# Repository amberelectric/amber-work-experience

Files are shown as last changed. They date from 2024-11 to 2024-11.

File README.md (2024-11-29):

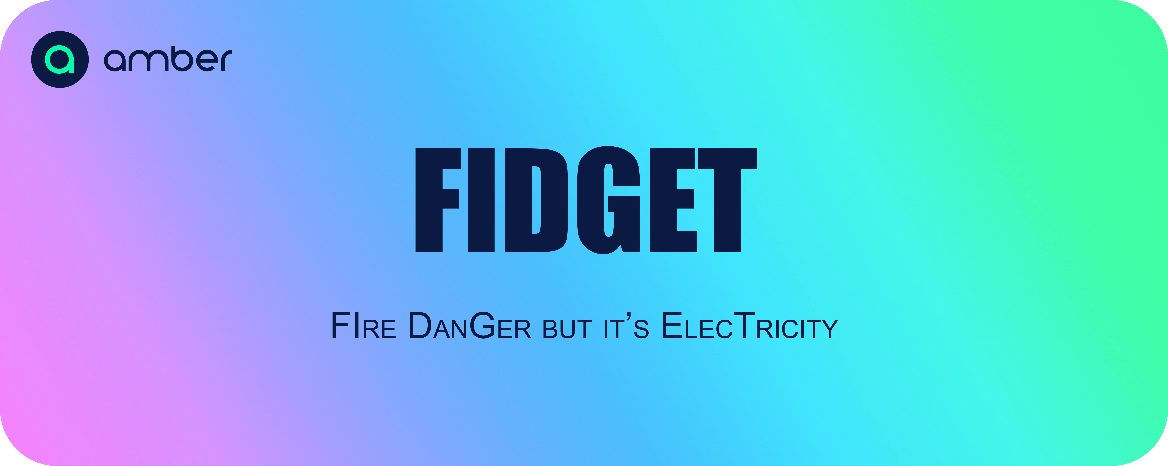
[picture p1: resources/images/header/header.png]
Amber FIDGET - Fire Danger but it's Electricity


# Intro / Say What Now?!

### What is it an what does it do?
The Amber FIDGET is a miniature Fire Danger Rating sign that displays the current power price descriptor for your house.

### How does it do it?
The FIDGET connects to your Wi-Fi network
and uses the [Amber API](https://app.amber.com.au/developers/documentation/)
to fetch the current price descriptor for your property.
It then translates this into a fire danger rating, and tells a servo motor to point at that rating, with 'tweening'.

# Build Guide

## Parts

### Owned
These parts are only needed to **make** the FIDGET. They are not required once it's running
- Computer (preferably should turn on)
- Hot Glue Gun
- 2D Printer
- 3D Printer (Not necessary. You can just tape or hot glue the components together.)
- Box Cutter
- Hair Dryer (I'll explain I promise)

### Purchased
Links are provided for Core Electronics, a Newcastle-based electronics provider with generally pretty good prices.
- [ESP32-C3 WROOM Dev Board](https://core-electronics.com.au/esp32-c3-wroom-development-board.html) (Or any other ESP32 board)
- [9g Micro Servo](https://core-electronics.com.au/feetech-fs90-1-5kgcm-micro-servo-9g.html) (Or any 9g servo with half-decent torque)
- [Male to Female Jumper Wires](https://core-electronics.com.au/jumper-wires-premium-12-m-f-pack-of-10.html) (Any wire will work but jumpers are nicer)
- [USB Micro-B Cable](https://core-electronics.com.au/usb-cable-type-a-to-micro-b-1m.html) (Once the FIDGET is running, it's possible to power it off a battery pack)

### Printed In Two Dimensions
The front of the sign has to be printed (or you can draw it, I guess).
If you have a colour printer, use `resources/images/sign/sign colour.png`.
Otherwise, use `resources/images/sign/sign bw.png` and colour in the sections with a pen or highlighter.

### Printed In Three Dimensions
Note: These parts are not strictly necessary, but they make putting together and pulling apart the FIDGET much easier.

The files you need to print are in the `resources/objects` folder.
`fire danger sign.f3d` is the Fusion 360 model for the entire FIDGET, and `fire danger sign.stl` is the whole model.
You only need to print `arrow.stl`, `servo bottom.stl`, `servo top.stl` and `esp32.stl`.

When printing, bigger layer heights are recommended to increase strength.

### Materials
- Cardboard box of regular thickness
- Hot glue
- Regular glue (tape will work too)
- Rubber band (a cable tie will work too)

## Make

### 1. Cut the Sign Cardboard
Use the box cutter to cut a piece of blank cardboard about half a centimeter bigger than the sign on all sides,
as shown in the picture below:

Cardboard cut about half a centimeter bigger than the sign on all sides

Then, align the sign in the center of the cardboard and glue it on.
Regular (non-hot) glue is preferable as it allows the paper to lie flush on the cardboard.

### 2. Wiring
The servo motor has to be connected to the ESP32 as follows:

| ESP32 Pin | Servo Pin |
|---|---|
| GND | - (Brown wire) |
| 5V | + (Red wire) |
| 0 | Signal (Orange wire) |

Note that you can use any of the GND or 5V pins on the ESP32.

### 3. Mount the Servo
To mount the servo on the sign you need to do a few things:
1. Use something sharp and pointy (pen, box cutter, scissors, drill, hole punch, etc) to punch a hole in the front of the sign where the servo will stick out.
2. If you 3D printed `servo top.stl` and `servo bottom.stl`:
   1. Place the servo inside `servo bottom`.
   2. Place `servo top` on top.
   3. Make sure the servo wire is out the side of the case, and the front of the servo protrudes from the front of the case.
   4. Carefully hot glue or melt the two halves of the servo case together, making sure not to get glue on the servo within.
3. Glue the servo case on to the back of the sign, so that the wires point to the left and the front of the servo goes through the hole in the sign.

The attached servo should look like the below image:

Mounted servo motor

### 4. Attach the Arrow
Turning around to the front of the sign, you can now attach the arrow to the servo motor.
In the bag of hardware that comes with the servo motor, there are five "horns" (pieces of plastic that attach to the gear on the front of the servo), one small screw and two large screws.

1. Make sure the servo is at 0˚. (Use the code at the end of this step)
2. Attach the **shortest** servo horn to the servo gear, pointing directly to the right. Note that it doesn't have to be pointing exactly right. You can adjust the angles it points to easily at the top of `main.cpp`.  
3. Screw the horn in place with the small screw.
4. Hot glue the arrow onto the horn.

To set the servo to 0˚, use the following code:
```c++
#include <ESP32_New_ISR_Servo.h>

void setup() {
  ESP32_ISR_Servos.useTimer(0);  // Use timer 0
  int servoIndex = ESP32_ISR_Servos.setupServo(0, 500, 2500);  // Start the servo on pin 0
  ESP32_ISR_Servos.setPosition(servoIndex, 0);  // Set the servo to 0˚
}

void loop() {}
```

The attached arrow should look like the below images:

Attached arrow
Attached arrow

### 5. Attach the ESP23
Attaching the ESP32 is fairly simple.
If you printed the ESP32 mount, hot glue it on the back of the FIDGET to the left, and clip in the ESP32.
If you didn't simply glue or tape the ESP32 in place.

Note:
The 3D printed mount may not fit perfectly.
Test it before you hot glue it in place and then bend the arms while they're hot from the glue.

The attached ESP32 should look like the below image:

Mounted ESP32

### 6. Finishing touches
Use a rubber band to hold the wires together neatly.
I feel like you shouldn't need an image for this one...

Then, cut out some more cardboard and hot glue it into a stand shape, like this:

FIDGET Stand

The design is primarily up to your imagination/engineering, but you should add a cross-beam to stop the cardboard from bending.

### 7. You did it!!
Congratulations!
You built the Amber FIDGET without blowing anything up!
Behold, the final product.
(The paperclip is because I had glue issues.)

Finished FIDGET
Finished FIDGET

# (Quick) Start

### Prerequisites
The only prerequisite for FIDGET is [PlatformIO Core](https://docs.platformio.org/en/latest/core/installation/index.html), a CLI for interfacing with the ESP32.

### Secrets file
FIDGET uses the Amber API to fetch the current price descriptor.
In order to accomplish this, you must have your WiFi and API credentials stored in `src/secrets.h`.
An example is provided below.

```c++
#define WIFI_SSID "[YOUR SSID]"
#define WIFI_PASSKEY "[YOUR PASSWORD]"
#define API_KEY "[YOUR API KEY]"
#define SITE_ID "[YOUR SITE ID]"
```

To find your Site ID, run the following command and look for the `id` key.

```sh
curl -H "Authorization: Bearer [YOUR API KEY]" https://api.amber.com.au/v1/sites
```

Note: If you are using the debug server, you must add the following line to `secrets.h` as well.

```c++
#define DEBUG_HOST "[YOUR IP ADDRESS OR HOSTNAME]"
```

### Quick Run
To quickly upload the code to the FIDGET, connect the ESP32 to your computer, then run `resources/scripts/upload.sh`.

# Usage

## Running the Code
Multiple scripts are provided in `resources/scripts`.
Each one serves a specific purpose:
- `compile.sh` checks that your code can be compiled for the ESP32 but does not upload the code.
- `upload.sh` compiles and uploads your code to the ESP32, then opens a serial monitor in your terminal.
- `debug.sh` starts the debugging server on your device.

Note:
Both `compile.sh` and `upload.sh` automatically install all required libraries via [the PlatformIO registry](https://registry.platformio.org).

## Troubleshooting

### Debug Server
To use the debug server, run `resources/debugServer.sh`, then enter your credentials when prompted.
This script will copy real-time data from the Amber API into `resources/v1/sites/[YOUR SITE ID]/prices/current`,
then start a local web server on port 8000 with Python's `http.server`.

On the ESP32 side,
all you need to do is define `DEBUG_HOST` in `secrets.h` (see "Secrets File")
and uncomment this line near the start of `main.cpp`:
```c++
#define USE_DEBUG_SERVER
```

## Logging
The following table shows the status messages displayed on the ESP32 LED and in the Serial Monitor.
A description of the state is in the `Status` column,
the LED colour and Serial output are shown in the next two columns,
and the final column shows the minimum required log level to show the state.

| Status | LED Colour | Print Statement | Level |
|---|---|---|---|
| Connecting to Wi-Fi | Yellow | Connecting to Wi-Fi... | Info |
| Setting Clock | Green | Setting time... | Info |
| Fetching Descriptor | Cyan | Fetching descriptor... | Info |
| Fetching Debug Descriptor | Blue | Fetching descriptor from debug server... | Info |
| Moving Servo | Purple | Updating servo... | Debug |
| Idle | White | Done! | Info |
| **Errors** | **Red-...** | | |
| Could not connect to Wi-Fi | Red-Red | Could not connect to Wi-Fi | Warning |
| Could not connect to the API | Red-Yellow-Red | Could not connect to API | Error |
| Could not configure API | Red-Yellow-Yellow | Could not configure API | Error |
| API timed out | Red-Yellow-Green  | API connection timed out | Error |
| API gave invalid response | Red-Yellow-Cyan | API returned invalid response | Error |
| HTTP status code error | Red-Green-Red | API returned error code: [CODE] | Error |
| HTTP could not skip headers | Red-Green-Yellow  | Could not skip HTTP headers: [CODE] | Error |
| Could not parse JSON | Red-Cyan-Red | Could not parse returned JSON | Error |
| Could not find general channel | Red-Cyan-Yellow | Could not find general channel in JSON | Error |
| Servo could not start | Red-Blue | Could not start servo | Fatal |
| Debug API not provided | Red-Purple | Debug API URL not provided. Using Amber API. | Warning |

Notes
1. Where more than one colour is listed in the `LED Colour` column,
   the LED will flash the colours in sequence with a 300ms delay.
2. The LED will show the appropriate colour no matter what the log level is set to.
3. If the `Level` is `Fatal`, the program will stop and the LED will flash the pattern repeatedly with a one second break.

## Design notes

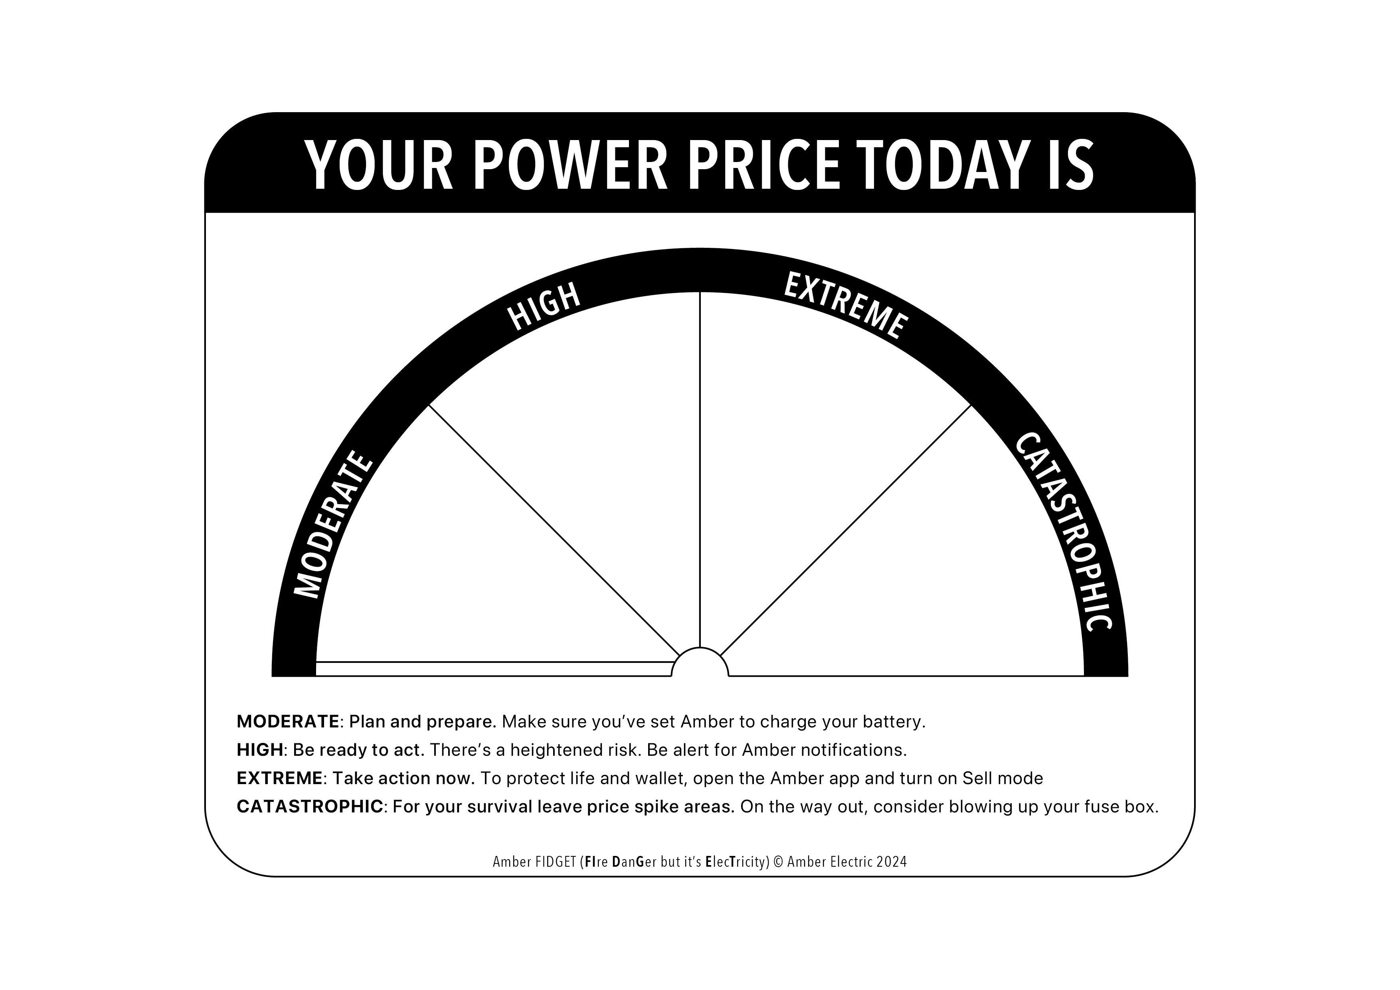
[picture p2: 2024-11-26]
resources/images/sign/sign bw.png

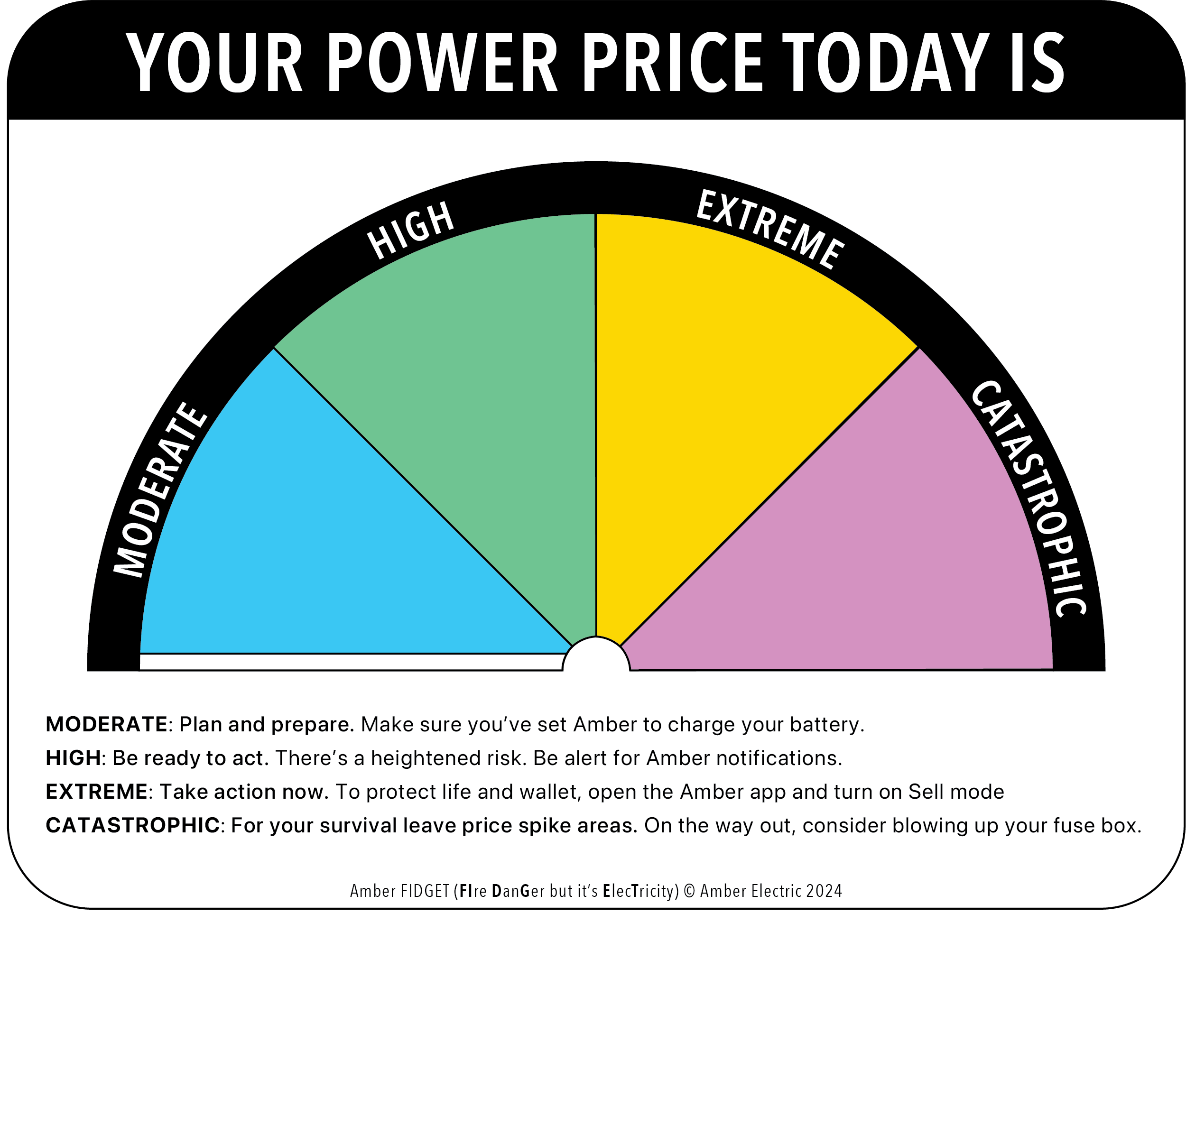
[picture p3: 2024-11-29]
resources/images/sign/sign colour.png

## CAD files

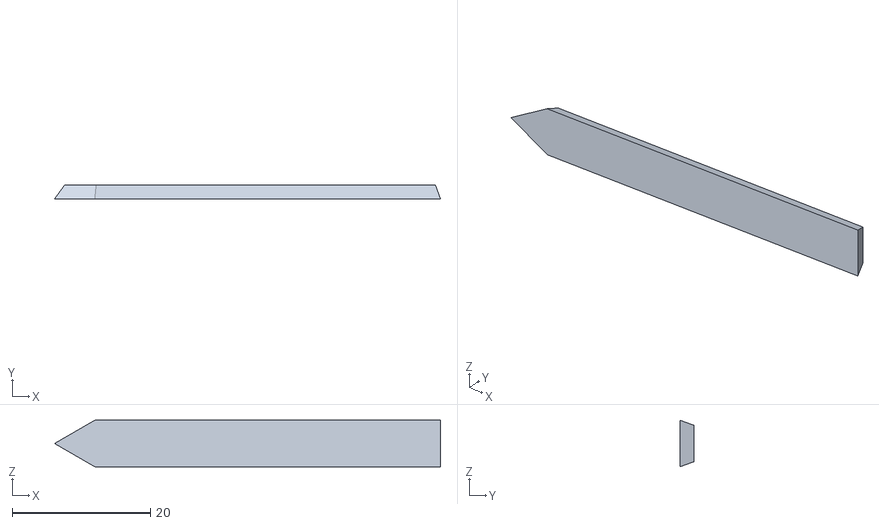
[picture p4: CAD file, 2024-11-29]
resources/objects/arrow.stl
55.8 x 2.00 x 6.73

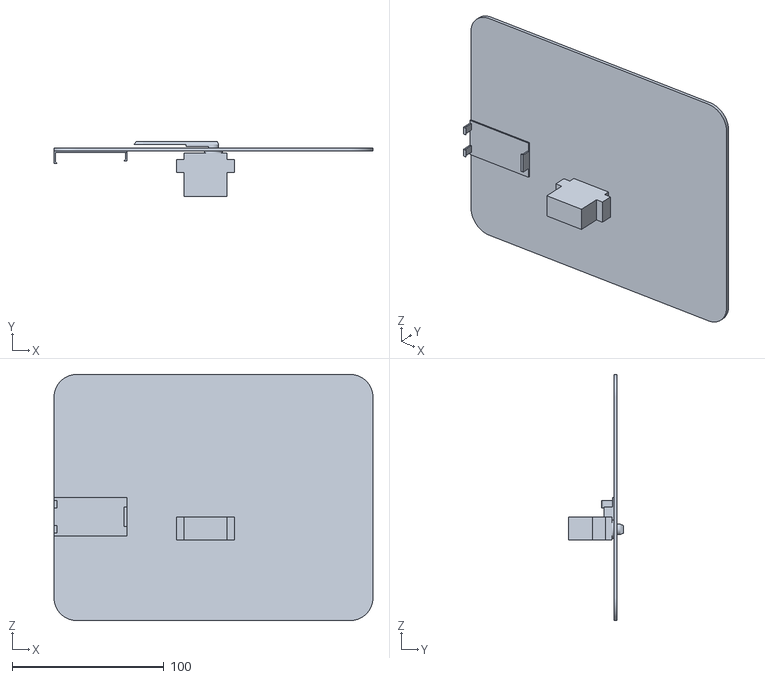
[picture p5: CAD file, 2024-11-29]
resources/objects/fire danger sign.stl
210.0 x 36.0 x 162.0

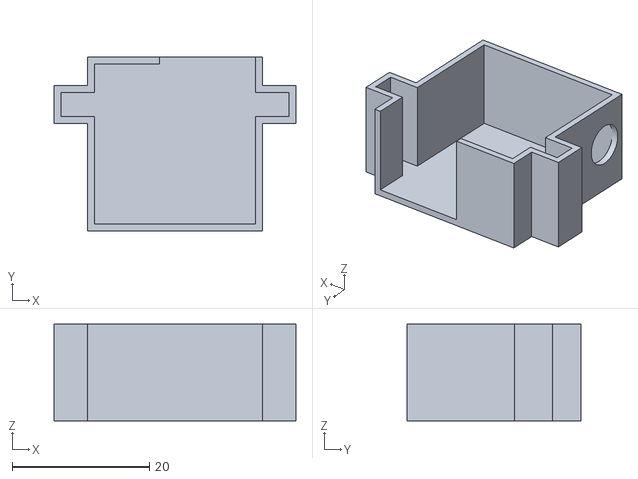
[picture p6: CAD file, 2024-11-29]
resources/objects/servo bottom.stl
35.3 x 25.4 x 14.1

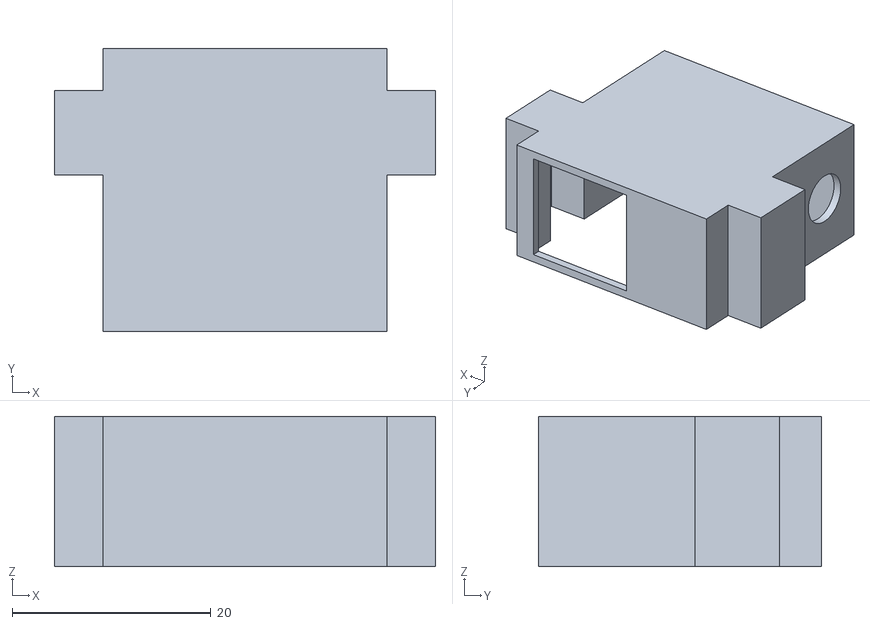
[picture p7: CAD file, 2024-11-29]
resources/objects/servo top.stl
38.3 x 28.4 x 15.1

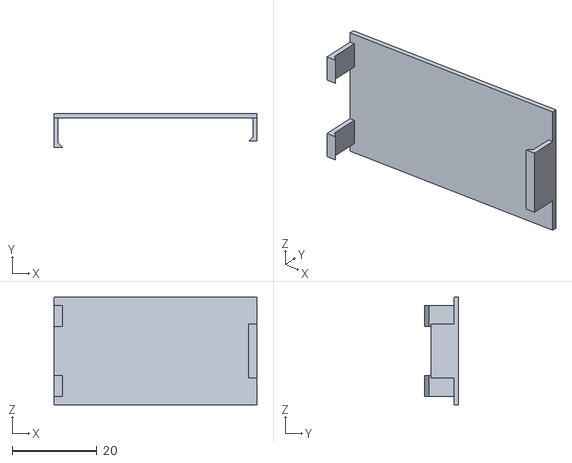
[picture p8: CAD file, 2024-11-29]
resources/objects/esp32.stl
48.0 x 8.00 x 25.5

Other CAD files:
resources/objects/fire danger sign.f3d

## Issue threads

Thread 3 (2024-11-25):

Move the servo

J-J-B-J, 2024-11-25:
The next step to making this is to make the ESP32 control the Servo motor based on the current price. The motor should point in the directions corresponding to the colours on a standard fire danger rating sign, as shown below:
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
To complete this, the following needs to be done:
- [x] Connect the Servo to the ESP32 and document how to do so
- [x] Find a library to drive the Servo
- [x] Figure out what angles to turn the Servo to based on what the price is and turn the Servo based on that amount.
- [x] Make a case for the ESP32 and Servo with the fire danger rating displayed.

Closed 2024-11-26.

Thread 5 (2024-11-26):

Setup a animation/tweening library, so we are able to smoothly move the servos

madpilot, 2024-11-26:
Rather than throwing the servo straight to the next angle, allow it to be moved smoothly.

1. See if you have find an off the shelf tweening library that will do the job. (timebox: 2 hours)
2. If you can't find something that is suitable, I have some hacky code tha will do it.

Bonus points if we can also animate the LED (smooth transition from one color to another, flash for errors etc)

Closed 2024-11-28.

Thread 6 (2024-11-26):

Bailout gracefully if the servo can't be initialised

madpilot, 2024-11-26:
This project is kind of useless if we can't initialise the servo.

If it does fail, flag an error state, and just flash an LED in the loop, rather than trying to hit the API

madpilot, 2024-11-28:
LGTM

Closed 2024-11-29.

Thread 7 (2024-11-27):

Debug API

J-J-B-J, 2024-11-27:
It's really hard to test different cases efficiently with the Amber API. There should be a simple Python API you can run locally to manually set the price descriptor, and a debug mode in the ESP32 code to point to it rather than the Amber API.

- [x] Make Python API
- [x] Make debug mode for ESP32

madpilot, 2024-11-27:
Protip. Python has a built in webserver that will serve up static files.

```
mkdir sites/$SITE_ID/prices
curl -H "Authorization: Bearer $API_KEY https://api.amber.com.au/sites/$SITE_ID/prices/current > sites/$SITE_ID/prices/current
python -m http.server
```

Then you can point to `$IP_ADDRESS:8080/sites/$SITE_ID/prices/current` and you haven't had to write any code. You just change the descriptor value in the JSON file that likes in the `sites/$SITE_ID/prices/current` file

J-J-B-J, 2024-11-27:
Thank you!!

Closed 2024-11-27.

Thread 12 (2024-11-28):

Servo Jiggling

J-J-B-J, 2024-11-28:
The servo has been jiggling randomly from side to side since I first started coding it, and I think I found the reason.

When you compile the code, the following warning appears:

```
In file included from .pio/libdeps/nodemcu-32s/ESP32_New_ISR_Servo/src/ESP32_New_ISR_Servo.h:49,
                 from src/main.cpp:6:
.pio/libdeps/nodemcu-32s/ESP32_New_ISR_Servo/src/ESP32_New_ISR_Servo.hpp:66:4: warning: #warning Using ESP32_C3-based board [-Wcpp]
   #warning Using ESP32_C3-based board
    ^~~~~~~
```

And since ESP32-C3 is a subtype of ESP32, I thought it would be fine to use the `ESP32_New_ISR_Servo` library. But I checked the [PlatformIO Registry](registry.platformio.org) and it turns out there's a library called `ESP32_C3_ISR_Servo` by the same author as `ESP32_New_ISR_Servo`, and my not using it may be the cause of the jiggling.

Even if it isn't the cause, it would still be a good idea to switch libraries for maximum compatibility.

J-J-B-J, 2024-11-29:
Turns out the currently used servo library does actually support the ESP32-C3. Also, I tried switching libraries, and it didn't fix the jiggling.

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

Due to this, this issue will not be fixed.

Closed 2024-11-29.

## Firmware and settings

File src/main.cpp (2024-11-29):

#include <Arduino.h>
#include <HttpClient.h>
#include <ArduinoJson.h>
#include <Adafruit_NeoPixel.h>
#include <Secrets.h>
#include <ESP32_New_ISR_Servo.h>
#include <Tween.h>

//#define USE_DEBUG_SERVER  // Uncomment this to use the local debugging API
#define LOG_LEVEL LOGGING_INFO

// Use http when on the debug server
#ifdef USE_DEBUG_SERVER
  #include <WiFiClient.h>
  #include <WiFi.h>
#else
  #include <WiFiClientSecure.h>
#endif

#define LED_PIN 8
#define NUMPIXELS 1

#define SERVO_PIN 1

#define BUFFER_SIZE 1024
#define WIFI_ATTEMPTS 10
#define TIMER_DELAY 300000

// Log levels
#define LOGGING_NONE    0
#define LOGGING_FATAL   1
#define LOGGING_ERROR   2
#define LOGGING_WARNING 3
#define LOGGING_INFO    4
#define LOGGING_DEBUG   5
#define LOGGING_VERBOSE 6

// LED colours
const int LED_NONE[]   = {  0,   0,   0};
const int LED_RED[]    = {255,   0,   0};
const int LED_YELLOW[] = {255, 255,   0};
const int LED_GREEN[]  = {  0, 255,   0};
const int LED_CYAN[]   = {  0, 255, 255};
const int LED_BLUE[]   = {  0,   0, 255};
const int LED_PURPLE[] = {255,   0, 255};
const int LED_WHITE[]  = {255, 255, 255};

// Servo angles
#define NO_DANGER           173
#define MODERATE_DANGER     150
#define HIGH_DANGER         108
#define SERVO_MIDPOINT       81
#define EXTREME_DANGER       58
#define CATASTROPHIC_DANGER  11

#define ANIMATION_SPEED 15  // Bigger numbers are slower

int servoIndex = -1;

Tween::Timeline timeline;
float target = 0.f;

int lastConnectionAttempt = 0;
#define CONNECT_DELAY 500

Adafruit_NeoPixel pixels(NUMPIXELS, LED_PIN, NEO_GRB + NEO_KHZ800);

void setLedColour(const int colour[3]) {
    pixels.clear();
    pixels.setPixelColor(0, pixels.Color(colour[0], colour[1], colour[2]));
    pixels.show();
}

void log(String text, int level, const int colour1[3], const int colour2[3]) {
  if (LOG_LEVEL >= level) {
    switch (level) {
      case LOGGING_FATAL:
        Serial.print("💥 Fatal Error: "); break;
      case LOGGING_ERROR:
        Serial.print("❗️ Error: "); break;
      case LOGGING_WARNING:
        Serial.print("⚠️ Warning: "); break;
      case LOGGING_INFO:
        Serial.print("ℹ️ Info: "); break;
      case LOGGING_DEBUG:
        Serial.print("🪲 Debug: "); break;
      case LOGGING_VERBOSE:
        Serial.print("Verbose: "); break;
    }
    Serial.println(text);
  }

  if (colour1 == LED_NONE) {
    return;
  }
  if (level == LOGGING_FATAL) {
    while (true) {
      setLedColour(LED_RED);
      delay(300);
      setLedColour(colour1);
      delay(300);
      if (colour2 != LED_NONE) {
        setLedColour(colour2);
        delay(300);
      }
      setLedColour(LED_NONE);
      delay(1000);
    }
  } else if (level <= LOGGING_WARNING) {
    setLedColour(LED_RED);
    delay(300);
  }
  setLedColour(colour1);
  if (colour2 != LED_NONE) {
    delay(300);
    setLedColour(colour2);
    delay(300);
    setLedColour(LED_NONE);
  }
}

void setClock() {
  configTime(0, 0, "pool.ntp.org");

  log(F("Setting time..."), LOGGING_INFO, LED_GREEN, LED_NONE);
  time_t nowSecs = time(nullptr);
  while (nowSecs < 8 * 3600 * 2) {
    delay(500);
    yield();
    nowSecs = time(nullptr);
  }

  struct tm timeinfo;
  gmtime_r(&nowSecs, &timeinfo);
  log(String(F("Current time: ")) + asctime(&timeinfo), LOGGING_VERBOSE, LED_NONE, LED_NONE);
}


unsigned long lastRun = 0;
bool connect()
{
  log(F("Connecting to Wi-Fi…"), LOGGING_INFO, LED_YELLOW, LED_NONE);

  if (WiFi.status() != WL_CONNECTED) {
    log(String(F("Could not connect to Wi-Fi")) + String(WiFi.status()), LOGGING_WARNING, LED_RED, LED_NONE);
    return false;
  }
  else
  {
    log(String(F("Connected to WiFi network with IP Address: ")) + WiFi.localIP(), LOGGING_VERBOSE, LED_NONE, LED_NONE);
    setClock();
    return true;
  }
}

String fetchDescriptor()
{
  #ifdef USE_DEBUG_SERVER
    WiFiClient client;
  #else
    WiFiClientSecure client;
    client.setInsecure();
  #endif

  HttpClient http(client);
  int err = 0;

  const char* server_name = "api.amber.com.au";
  uint16_t port = 443;

  #ifdef USE_DEBUG_SERVER
    #ifdef DEBUG_HOST
      log(F("Fetching descriptor from debug server..."), LOGGING_INFO, LED_BLUE, LED_NONE);
      server_name = DEBUG_HOST;
      port = 8000;
    #else
      log(F("Debug API URL not provided. Using Amber API."), LOGGING_WARNING, LED_PURPLE, LED_NONE);
      delay(500);
    #endif
  #endif

  if (server_name == "api.amber.com.au") {log(F("Fetching descriptor..."), LOGGING_INFO, LED_CYAN, LED_NONE);}

  String path = String("/v1/sites/") + String(SITE_ID) + String("/prices/current");

  http.beginRequest();
  err = http.startRequest(server_name, port, path.c_str(), HTTP_METHOD_GET, "AmberFidget");
  if (err != HTTP_SUCCESS)
  {
    switch (err)
    {
    case HTTP_ERROR_CONNECTION_FAILED:
      log(F("Could not connect to API"), LOGGING_ERROR, LED_YELLOW, LED_RED);
      break;
    case HTTP_ERROR_API:
      log(F("Could not configure API"), LOGGING_ERROR, LED_YELLOW, LED_YELLOW);
      break;
    case HTTP_ERROR_TIMED_OUT:
      log(F("API connection timed out"), LOGGING_ERROR, LED_YELLOW, LED_GREEN);
      break;
    case HTTP_ERROR_INVALID_RESPONSE:
      log(F("API returned invalid response"), LOGGING_ERROR, LED_YELLOW, LED_CYAN);
      break;
    }
    http.stop();
    return "";
  }

  String bearerToken = String("Bearer ") + String(API_KEY);
  http.sendHeader("Authorization", bearerToken.c_str());
  http.endRequest();

  err = http.responseStatusCode();
  if (err != 200)
  {
    log(String(F("API returned error code: ")) + String(err), LOGGING_ERROR, LED_GREEN, LED_RED);
    http.stop();
    return String("");
  }

  err = http.skipResponseHeaders();
  if (err != HTTP_SUCCESS)
  {
    log(String(F("Could not skip HTTP headers: ")) + String(err), LOGGING_ERROR, LED_GREEN, LED_YELLOW);
    http.stop();
    return String("");
  }

  unsigned long timeoutStart = millis();
  char json[BUFFER_SIZE];
  memset((char *)&json, 0, BUFFER_SIZE);
  int i = 0;
  // Leave one character at the end, so the string is always terminated
  while (i < BUFFER_SIZE - 1 && (http.connected() || http.available()) && ((millis() - timeoutStart) < 30000))
  {
    if (http.available())
    {
      json[i++] = http.read();
      // Print out this character
      // We read something, reset the timeout counter
      timeoutStart = millis();
    }
    else
    {
      // We haven't got any data, so let's pause to allow some to
      // arrive
      delay(1000);
    }
  }

  http.stop();

  StaticJsonDocument<BUFFER_SIZE> doc;
  deserializeJson(doc, (char *)&json);
  if (!doc.is<JsonArray>())
  {
    log(F("Could not parse returned JSON"), LOGGING_ERROR, LED_CYAN, LED_RED);
    return String("");
  }

  JsonArray prices = doc.as<JsonArray>();
  for (JsonVariant p : prices)
  {
    if (p.is<JsonObject>())
    {
      JsonObject price = p.as<JsonObject>();
      String channelType = price["channelType"].as<String>();
      if (channelType == "general")
      {
        return price["descriptor"].as<String>();
      }
    }
  }

  log(F("Could not find general channel in JSON"), LOGGING_ERROR, LED_CYAN, LED_YELLOW);
  return String("");
}

void sequence_motions(float newTarget) {
  log(F("Updating servo"), LOGGING_DEBUG, LED_PURPLE, LED_NONE);
  if (target == newTarget) {
    return;
  }
  timeline.clear();
  timeline.add(target);

  // Big complex decision tree
  // If the current and desired servo position are on the same side, AND the current position is closer to the
  // top (≈90˚), then bounce "down" (away from 90˚). OTHERWISE, just back in/out.
  if (target < SERVO_MIDPOINT) {
    if (newTarget < SERVO_MIDPOINT && target > newTarget) {
      timeline[target].then<Ease::BounceOut>(newTarget, (target - newTarget) * ANIMATION_SPEED);
    } else {
      timeline[target].then<Ease::BackInOut>(newTarget, abs(target - newTarget) * ANIMATION_SPEED * 2);
    }
  } else {
    if (newTarget > SERVO_MIDPOINT && target < newTarget) {
      timeline[target].then<Ease::BounceOut>(newTarget, (newTarget - target) * ANIMATION_SPEED);
    } else {
      timeline[target].then<Ease::BackInOut>(newTarget, abs(newTarget - target) * ANIMATION_SPEED * 2);
    }
  }
  timeline.start();
}

void setup()
{
  Serial.begin(115200);
  WiFi.begin(WIFI_SSID, WIFI_PASSKEY);

  // Set up the servo
  ESP32_ISR_Servos.useTimer(0);
  servoIndex = ESP32_ISR_Servos.setupServo(0, 500, 2500);
  if (servoIndex == -1) {
    log(F("Could not start servo"), LOGGING_FATAL, LED_BLUE, LED_NONE);
  }
  timeline.add(target)
    .init(SERVO_MIDPOINT)
    .offset(1000)
    .then<Ease::BounceOut>(NO_DANGER, 2000);
  timeline.start();

  // Force a run 5000ms after startup (to allow servo animation to complete)
  lastRun = 5000 - TIMER_DELAY;

  pixels.begin();
}

void loop()
{
  // Update the servo position as set by the tweening library
  timeline.update();
  ESP32_ISR_Servos.setPosition(servoIndex, target);

  // Connect to WiFi
  if (WiFi.status() != WL_CONNECTED)  {
    if ((millis()-lastConnectionAttempt) < CONNECT_DELAY) {
      return;
    }
    if (!(((millis()-lastConnectionAttempt) > CONNECT_DELAY) && connect())) {
        Serial.println("WiFi connection not acquired yet. Trying again soon...");
        lastConnectionAttempt = millis();
        return;
    }
  }

  if ((millis() - lastRun) > TIMER_DELAY)  {
    String descriptor = fetchDescriptor();

    if (descriptor != String(""))
    {
      log(String(F("Current Price Descriptor: ")) + descriptor, LOGGING_VERBOSE, LED_NONE, LED_NONE);

      if (descriptor == String("spike"))
      {
        log(F("Price Spike!"), LOGGING_VERBOSE, LED_NONE, LED_NONE);
        sequence_motions(CATASTROPHIC_DANGER);
      }
      else if (descriptor == String("high"))
      {
        log(F("High prices"), LOGGING_VERBOSE, LED_NONE, LED_NONE);
        sequence_motions(CATASTROPHIC_DANGER);
      }
      else if (descriptor == String("neutral"))
      {
        log(F("Average prices"), LOGGING_VERBOSE, LED_NONE, LED_NONE);
        sequence_motions(EXTREME_DANGER);
      }
      else if (descriptor == String("low"))
      {
        log(F("Low prices"), LOGGING_VERBOSE, LED_NONE, LED_NONE);
        sequence_motions(HIGH_DANGER);
      }
      else if (descriptor == String("veryLow"))
      {
        log(F("Very Low prices"), LOGGING_VERBOSE, LED_NONE, LED_NONE);
        sequence_motions(MODERATE_DANGER);
      }
      else
      {
        log(F("Extremely low prices"), LOGGING_VERBOSE, LED_NONE, LED_NONE);
        sequence_motions(MODERATE_DANGER);
      }
    }

    lastRun = millis();
    log(F("Done!"), LOGGING_INFO, LED_WHITE, LED_NONE);
  }
}

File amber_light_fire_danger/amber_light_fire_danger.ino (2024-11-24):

#include <WiFiClientSecure.h>
#include <HttpClient.h> // From https://github.com/amcewen/HttpClient
#include <ArduinoJson.h>
#include <Adafruit_NeoPixel.h>

#define WIFI_SSID "[WIFI AP NAME HERE]"
#define WIFI_PASSKEY "[WIFI PASSKEY NAME HERE]"
#define API_KEY "[AMBER API KEY HERE]"
#define SITE_ID "[AMBER SITE ID KEY HERE]" // To get this, run `curl -H "Authorization: Bearer [AMBER_API_KEY] https://api.amber.com.au/v1/sites" and look for the id

#define PIN 8
#define NUMPIXELS 1

#define BUFFER_SIZE 1024
#define WIFI_ATTEMPTS 10
#define TIMER_DELAY 300000

Adafruit_NeoPixel pixels(NUMPIXELS, PIN, NEO_GRB + NEO_KHZ800);

void setClock() {
  configTime(0, 0, "pool.ntp.org");

  Serial.print(F("Waiting for NTP time sync: "));
  time_t nowSecs = time(nullptr);
  while (nowSecs < 8 * 3600 * 2) {
    delay(500);
    Serial.print(F("."));
    yield();
    nowSecs = time(nullptr);
  }

  Serial.println();
  struct tm timeinfo;
  gmtime_r(&nowSecs, &timeinfo);
  Serial.print(F("Current time: "));
  Serial.print(asctime(&timeinfo));
}


unsigned long lastRun = 0;
bool connect()
{
  Serial.print("Connecting to WiFi");
  int attempts = 0;

  while (WiFi.status() != WL_CONNECTED && attempts < WIFI_ATTEMPTS)
  {
    delay(500);
    Serial.print(".");
    attempts++;
  }

  Serial.println("");

  if (attempts == WIFI_ATTEMPTS)
  {
    Serial.println("Unable to connect to the WiFi");
    return false;
  }
  else
  {
    Serial.print("Connected to WiFi network with IP Address: ");
    Serial.println(WiFi.localIP());
    setClock();  
    return true;
  }
}

String fetchDescriptor()
{
  WiFiClientSecure client;
  client.setInsecure();
  HttpClient http(client);
  int err = 0;

  String path = String("/v1/sites/") + String(SITE_ID) + String("/prices/current");

  http.beginRequest();
  err = http.startRequest("api.amber.com.au", 443, path.c_str(), HTTP_METHOD_GET, "ArduinoAmberLight");
  if (err != HTTP_SUCCESS)
  {
    switch (err)
    {
    case HTTP_ERROR_CONNECTION_FAILED:
      Serial.println("ERROR: Unable to connect to the API");
      break;
    case HTTP_ERROR_API:
      Serial.println("ERROR: Configuration issue");
      break;
    case HTTP_ERROR_TIMED_OUT:
      Serial.println("ERROR: Connection timed out");
      break;
    case HTTP_ERROR_INVALID_RESPONSE:
      Serial.println("ERROR: Invalid response received");
      break;
    }
    http.stop();
    return "";
  }

  String bearerToken = String("Bearer ") + String(API_KEY);
  http.sendHeader("Authorization", bearerToken.c_str());
  http.endRequest();

  err = http.responseStatusCode();
  if (err != 200)
  {
    Serial.printf("ERROR: Received Status Code: %d\n", err);
    http.stop();
    return String("");
  }

  err = http.skipResponseHeaders();
  if (err != HTTP_SUCCESS)
  {
    Serial.printf("ERROR: Unable to skip headers: %d\n", err);
    http.stop();
    return String("");
  }

  unsigned long timeoutStart = millis();
  char json[BUFFER_SIZE];
  memset((char *)&json, 0, BUFFER_SIZE);
  int i = 0;
  // Leave one character at the end, so the string is always terminated
  while (i < BUFFER_SIZE - 1 && (http.connected() || http.available()) && ((millis() - timeoutStart) < 30000))
  {
    if (http.available())
    {
      json[i++] = http.read();
      // Print out this character
      // We read something, reset the timeout counter
      timeoutStart = millis();
    }
    else
    {
      // We haven't got any data, so let's pause to allow some to
      // arrive
      delay(1000);
    }
  }

  http.stop();

  StaticJsonDocument<BUFFER_SIZE> doc;
  deserializeJson(doc, (char *)&json);
  if (!doc.is<JsonArray>())
  {
    Serial.println("Returned JSON object is not an array");
    return String("");
  }

  JsonArray prices = doc.as<JsonArray>();
  for (JsonVariant p : prices)
  {
    if (p.is<JsonObject>())
    {
      JsonObject price = p.as<JsonObject>();
      String channelType = price["channelType"].as<String>();
      if (channelType == "general")
      {
        return price["descriptor"].as<String>();
      }
    }
  }

  Serial.println("Error: General channel not found");
  return String("");
}

void setup()
{
  Serial.begin(115200);
  WiFi.begin(WIFI_SSID, WIFI_PASSKEY);
  // Force a run on startup
  lastRun = TIMER_DELAY;
  pixels.begin();
}

void loop()
{
  if (WiFi.status() != WL_CONNECTED && !connect())
  {
    Serial.println("WiFi connection attempts timed out. Will try again in a second.");
    delay(1000);
    return;
  }


  if ((millis() - lastRun) > TIMER_DELAY)
  {
    Serial.println("Checking the price");
    String descriptor = fetchDescriptor();

    pixels.clear();
    if (descriptor != String(""))
    {
      Serial.printf("Current Descriptor: %s\n", descriptor);
      
      if (descriptor == String("spike"))
      {
        Serial.printf("Price Spike!\n");
        pixels.setPixelColor(0, pixels.Color(255, 0, 255));
      }
      else if (descriptor == String("high"))
      {
        Serial.printf("High prices\n");
        pixels.setPixelColor(0, pixels.Color(255, 0, 0));
      }
      else if (descriptor == String("neutral"))
      {
        Serial.printf("Average prices\n");
        pixels.setPixelColor(0, pixels.Color(255, 165, 0));
      }
      else if (descriptor == String("low"))
      {
        Serial.printf("Low prices\n");
        pixels.setPixelColor(0, pixels.Color(255, 255, 0));
      }
      else if (descriptor == String("veryLow"))
      {
        Serial.printf("Very Low prices\n");
        pixels.setPixelColor(0, pixels.Color(0, 255, 0));
      }
      else
      {
        Serial.printf("Extremely low prices\n");
        pixels.setPixelColor(0, pixels.Color(0, 255, 255));
      }
    }
    pixels.show();

    lastRun = millis();
  }
}

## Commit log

2024-11-25 Convert project to PlatformIO
    Switched project format from standard Arduino project to PlatformIO, and installed necessary libraries.
2024-11-25 Make run workflow for JetBrains IDEs
    The "Upload" configuration will run "run.sh" which will automatically build and upload the code to the ESP32, then open the Serial Monitor.
2024-11-25 Make servo move based on price descriptor
    The servo is now connected to pin 0 on the ESP32 and moves to a set angle based on the current price descriptor fetched from the Amber API. The angles correspond to a fire danger rating sign.
2024-11-25 Update README with servo instructions
    Added instructions in README.md on what parts to use for the project, and how to connect the servo motor to the ESP32.
2024-11-26 Update servo angles
    Fix servo angles so that they match the sign properly.
    [main.cpp]
2024-11-26 Create Fire Danger Sign.f3d
    Added the Fusion 360 model for the sign to the `resources` folder.
    [Fire Danger Sign.f3d]
2024-11-27 Make WiFi connection semi-asynchronous
    Adjusted the `connect()` function so that it doesn't block the `loop()`.
    [main.cpp]
2024-11-27 Make debug server mode on ESP32
    Made a single line that controls whether the ESP32 uses the Amber API or the debug server
2024-11-27 Add servo tweening for moving between levels
    Used the `Tween` library to make the servo motor move smoothly between the different levels
2024-11-28 Add better comments for decision making and math
    Explain the decisions behind the servo animations, and the 5000ms API call delay at the start.
2024-11-29 Replace Serial.println statements with logging
    Replaced the `Serial.println()` statements with `log()`. Also added verbosity modes, and removed calls to methods of `pixels`.
    [main.cpp]
2024-11-29 Print log lev for log statements
    Added fun statements at the start of logs that display the log level.
2024-11-29 Make LED show status
    Made the LED show colours based on the protocol in #6
2024-11-29 Add parts instructions to README
    Added the parts list to the README, as well as reorganising the resources folder to be more intuitive
    [arrow.stl, esp32.stl, fire danger sign.f3d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]
2024-11-29 Rotate cut cardboard.png
    So it's actually the right way up!
